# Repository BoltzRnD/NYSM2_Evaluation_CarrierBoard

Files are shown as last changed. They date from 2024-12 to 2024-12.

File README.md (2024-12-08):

# NYSM.2 Evaluation Carrier Board

### Note - This repository hosts the design files for the evaluation carrier board only, to explore the NYSM.2 Stepper Driver module please refer to NYSM.2 repository here -
<a href="https://github.com/BoltzRnD/NYSM2_Open_Stepper_Standard">NYSM.2 Open Modular Stepper Driver Interface Standard by Boltz R&D </a>
</br>

### Join our Discord Server to Discuss NYSM.2 -



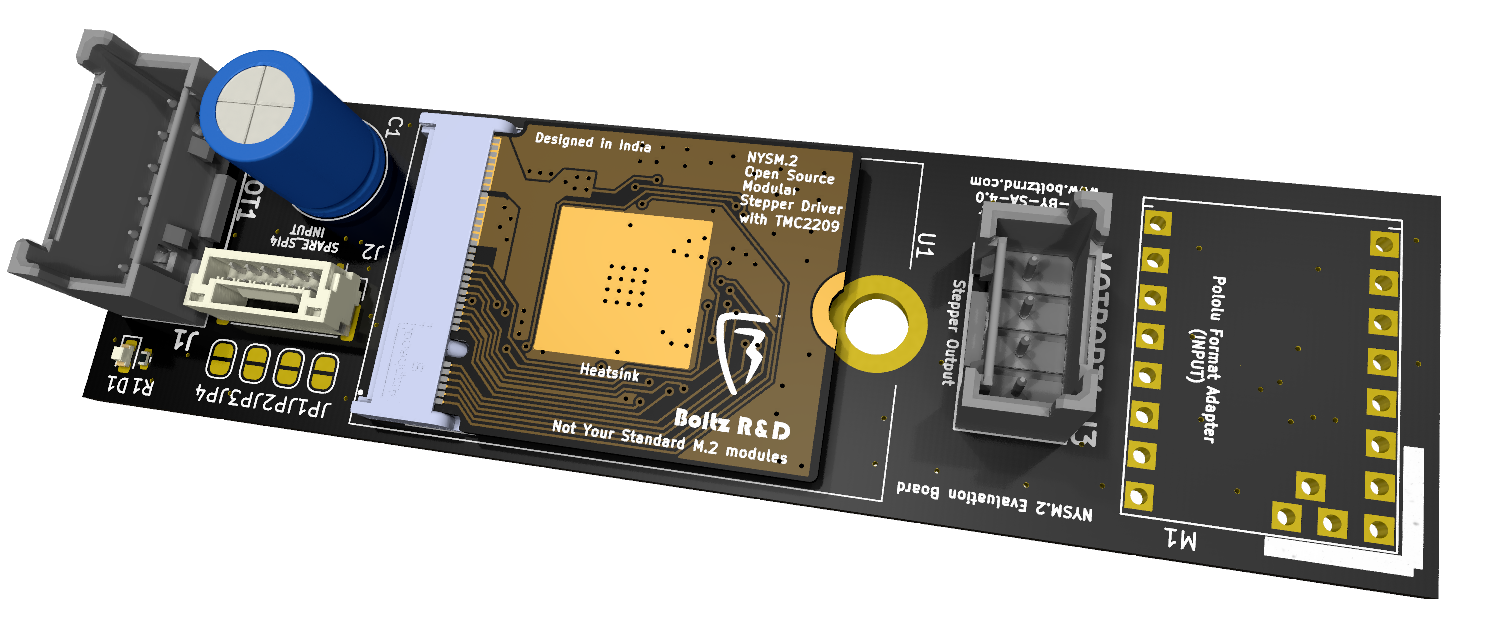
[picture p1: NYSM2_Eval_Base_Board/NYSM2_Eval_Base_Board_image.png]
NYSM.2


# NYSM.2 Open Stepper Standard
## Not Your Standard M.2
### "Not Your Standard M.2" is literally not your standard m.2 interface, and is a new open-source stepper motor driver board that utilizes the M.2 interface to control motors using the TMCxx and all other stepper drivers.

Modular stepper drivers are far superior than traditional pololu footprints as it has

1. Poka-yoke installations: The Key's in the interfaces makes sure that you never mess up installation orientations of the driver

apart from this NYSM.2 extends beyond these to provide more features as below:

1. physical locking mechanisms: to make sure drivers are locked in when In operation.

2. Horizontal installation: instead of vertical mounting, to not only save space in Z axis, but to also make the system less fragile to accidental damage if stuck by a physical shock.

3. Top and Bottom Installations: since NYSM.2 utilizes SMD and single layer mounted connectors, it means that it is possible to add by design 2 NYSM.2 modules in the same footprint area, drastically reducing the required footprint for more drivers - i.e - 20 drivers in 10 drivers area by installing 10 on top layer and 10 on bottom.

4. highly cost effective: since M.2 is a widely available standard with high MOQs already flooding the industry, the M.2 connectors can be integrated at very low costs into your design, where the stepper card doesn't even need a connector as it uses an edge connector built into the PCB only. in comparison to other modular standards that uses custom repurposed obsolete connector that has low manufacturing volumes. With NYSM.2 we can adopt a modular standard at almost same cost of a traditional pololu stepper drivers.

5. Powerful in terms of power: NYSM.2 utilizes 8 contacts(0.5A per pin) per power connection to deliver a whopping **4A** to the motors, that too at **24V**, that totals to **96W** per driver.
moreover it is theoretically possible to get more power out of it by increasing the voltages.

But that is not the best thing about NYSM.2 standard, the only best thing about it is only and only it's open source nature and GPL V3 license, that allows creators, hobbyist and manufacturers worldwide to move to a new and open modular stepper driver interface standard.
unlike other modular stepper interfaces, this interface is open inside out, and is not designed to lock you into single specific manufacturer's ecosystem. and is made for the world to use.

## The NYSM.2 Standard Pinout Format

## Pinout Table

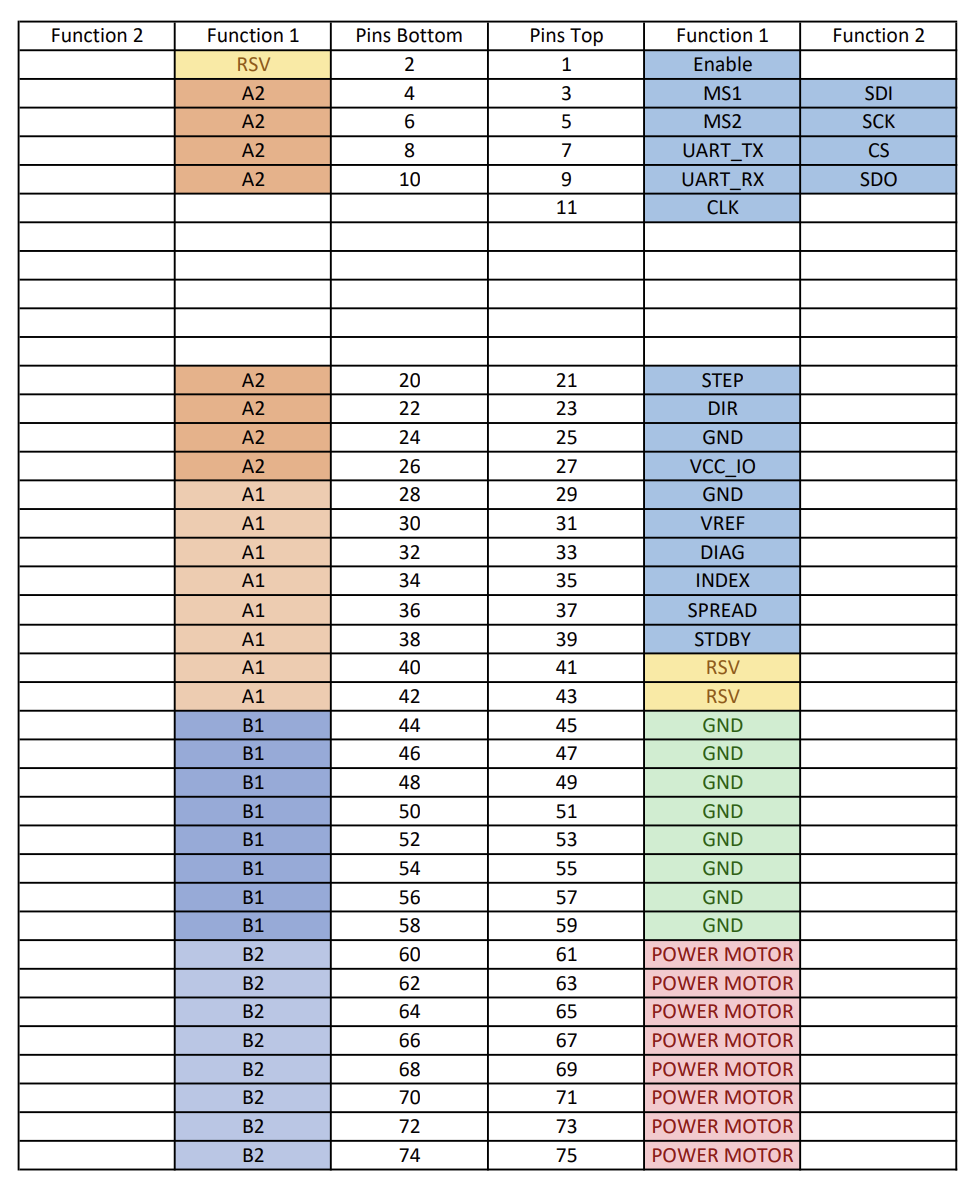
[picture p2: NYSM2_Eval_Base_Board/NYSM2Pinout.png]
NYSM.2 Pinout


| Pin Name | Pin Number | Description 
|---|---|---|
| EN | 1 | Enable/Disable Stepper Driver
| MS1 | 3 | Microstep Selection Pin 1 / CFG1 / SDI
| MS2 | 5 | Microstep Selection Pin 2 / CFG2 / SCK
| UART_TX | 7 | UART Transmission (Communication) / CFG 3 / CS
| UART_RX | 9 | UART Receive (Communication) / CFG0 / SDO
| CLK | 11 | CLK input 
| STEP | 21 | STEP input 
| DIR | 23 | DIR input 
| GND | 25 | Ground 
| VCC_IO | 27 | 3.3V to 5V IO supply voltage for all digital pins (does not supply IC logic part).
| GND | 29 | Ground 
| VREF | 31 | Analog reference voltage for current scaling or reference current for use of internal sense resistors
| DIAG | 33 | Diagnostic and StallGuard output
| INDEX | 35 | Configurable index output. Provides index pulse.
| SPREAD | 37 | Chopper mode selection: Low=StealthChop, High=SpreadCycle (may be left unconnected)
| STDBY | 39 | STANDBY input  
| GND | 45, 47, 49, 51, 53, 55, 57, 59 | Ground/PSU Negative (0.5A per pin, 4A Total)
| POW_MOT | 61, 63, 65, 67, 69, 71, 73, 75 | Motor supply voltage (0.5A per pin, 4A Total)
| A2 | 4, 6, 8, 10, 20, 22, 24, 26 | Motor coil A output 2 (0.5A per pin, 4A Total)
| A1 | 28, 30, 32, 34, 36, 38, 40, 42 | Motor coil A output 1 (0.5A per pin, 4A Total)
| B1 | 44, 46, 48, 50, 52, 54, 56, 58 | Motor coil B output 1 (0.5A per pin, 4A Total)
| B2 | 60, 62, 64, 66, 68, 70, 72, 74 | Motor coil B output 2 (0.5A per pin, 4A Total)

# Manufacturing and other design considerations

Please take special care to follow these points when manufacturing the NYSM2 Boards
1. You'll need Connector assemblies to interface the board specifically - GHR-06V-S and 511630400 Connectors, which are the same cables used in SmartPrintCoreH7x, please refer to Connector BOM from SmartPrintCoreH7x for more details
2. Set the solder jumpers as per your convenience especially for uart lines, just like your regular pololu drivers, please feel free to browse schematics for reference or directly reach out to our discord server for help.

# License
NYSM.2 standard pinout and NYSM.2 TMC2209 Carrier Board contributed by Boltz R&D is licensed under GPL V3, and is owned by the community and everyone.
Also while the standard is open(i.e - The standard pinout sequence on M.2 Key B and it's derivatives only, that means proprietary manufacturers needs to be compliant to GPLV3 for only the pinout.),
you can integrate it into your proprietary designs as long as the NYSM.2 section of your design respects the license.
We invite all creators, hobbyist, and manufacturers to utilize the standard and the design.

# Key Features for this NYSM.2 Carrier Board:
* NYSM.2 Interface: Compact, modular design that fits into M.2 slots, making it easy to install and maintain.
* The Connectors and pinouts used in the design plugs directly into Smartmotor ports and any SPI Port of SmartPrintCoreH7x, and with just minor pinout configurations in the firmware, it's up and running.

## Assembly and Setup

1. **Step 1**: Insert the **NYSM.2** board into the M.2 slot.
2. **Step 2**: Connect your stepper motor wires to the appropriate output terminals i.e- Smartmotor ports and any spi port(which can also act as a uart port).
3. **Step 3**: Configure your firmware (e.g., **Marlin** or **Klipper**) to control the TMC2209 driver.
4. **Step 4**: Power on the system, and your motors are ready.

## Getting Started on Development:

Clone the repository:  
`git clone https://github.com/BoltzRnD/NYSM2_Evaluation_CarrierBoard`

# Join the Community
We are actively looking for contributors to help us enhance this project. You can join our community to discuss ideas, report bugs, or request features:

- **Discord**: [Join us here](https://discord.gg/xWGaHd83Hs)
- **Email**: info@boltzrnd.com

# Future Plans
- **Custom Heatsink Designs**.
- **Extended Compatibility**: support for other stepper driver like TMC5160 and TMC2130.

# Disclaimer
The **NYSM.2 standard and NYSM.2 Carrier board** is provided as-is without any warranties. Boltz R&D is not responsible for any damages or issues that may arise from the use of this board.

    NYSM.2 standard
    Copyright (C) 2024 Boltz R&D

    This Project/Open Standard is free: you can redistribute it and/or modify
    it under the terms of the GNU General Public License as published by
    the Free Software Foundation, either version 3 of the License, or
    (at your option) any later version.

    This is distributed in the hope that it will be useful,
    but WITHOUT ANY WARRANTY; without even the implied warranty of
    MERCHANTABILITY or FITNESS FOR A PARTICULAR PURPOSE.  See the
    GNU General Public License for more details.

    You should have received a copy of the GNU General Public License
    along with this program.  If not, see <https://www.gnu.org/licenses/>.

Contact : info@boltzrnd.com

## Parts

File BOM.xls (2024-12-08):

Comment | Designator | Footprint | JLCPCB Part #
MOTPORT1 | J3 | connectorslibrary:53375-0410 | C327537
SMRTMOT1 | J1 | connectorslibrary:53375-0610 | C504969
~ | U1 | MDT275B03001:AMPHENOL_MDT275B03001 | C2761344
M2Mount | H1 | M2Mount | C5301790
POW-MOT | D1 | LED_SMD:LED_0603_1608Metric | C72038
4.7K | R1 | Resistor_SMD:R_0402_1005Metric | C140158
SPARE_SPI4 | J2 | Connector_JST:JST_GH_BM06B-GHS-TBT_1x06-1MP_P1.25mm_Vertical | C189892
100uF50V | C1 | Capacitor_THT:C_Radial_D8.0mm_H11.5mm_P3.50mm | C2960238

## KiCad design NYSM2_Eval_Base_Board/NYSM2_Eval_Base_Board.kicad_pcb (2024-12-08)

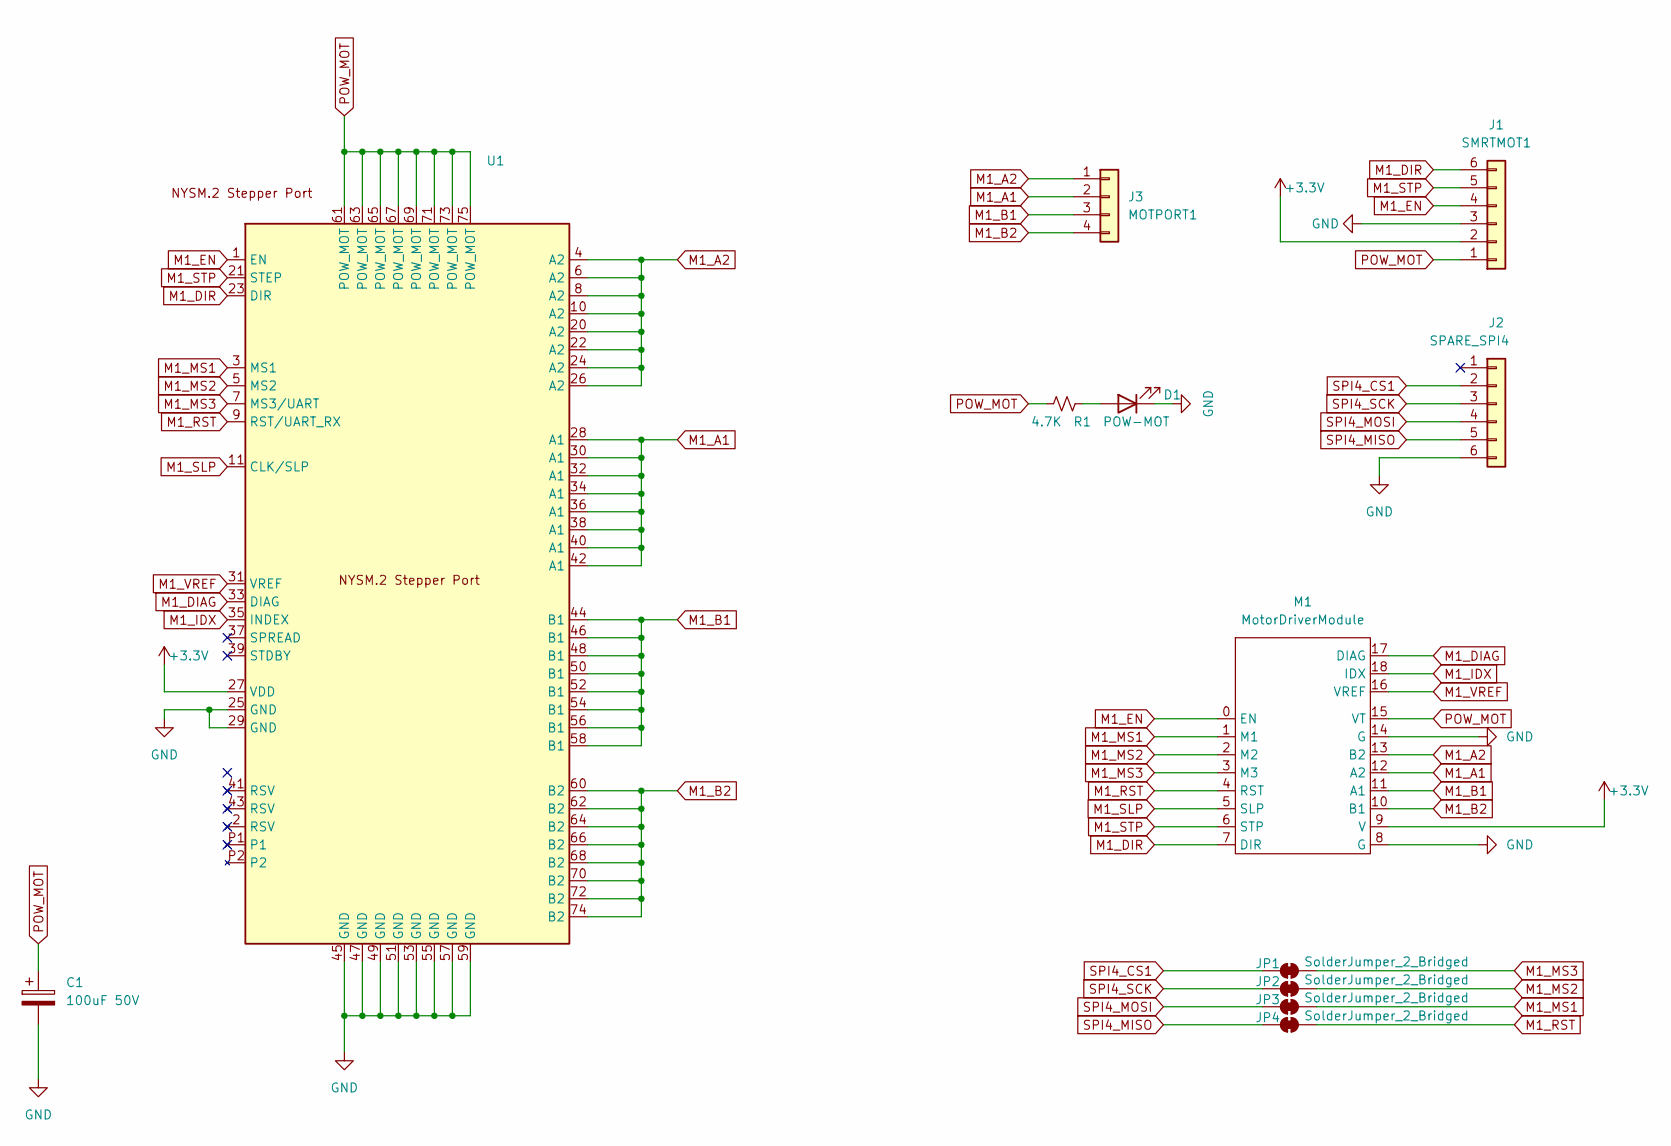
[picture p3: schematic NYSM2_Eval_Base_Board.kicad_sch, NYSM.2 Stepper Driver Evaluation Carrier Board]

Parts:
C1: 100uF 50V; C_Radial_D8.0mm_H11.5mm_P3.50mm
D1: POW-MOT; LED_0603_1608Metric; Manufacturer_Part_Number B1911PG--20D000514U1930
J1: SMRTMOT1; 53375-0610; Manufacturer_Part_Number 53375-0610
J2: SPARE_SPI4; JST_GH_BM06B-GHS-TBT_1x06-1MP_P1.25mm_Vertical; Manufacturer_Part_Number BM06B-GHS-TBT
J3: MOTPORT1; 53375-0410; Manufacturer_Part_Number 53375-0410
JP1, JP2, JP3, JP4: SolderJumper_2_Bridged; SolderJumper-2_P1.3mm_Bridged_RoundedPad1.0x1.5mm
M1: MotorDriverModule; MotorDriverModuleBase
R1: 4.7K; R_0402_1005Metric; Manufacturer_Part_Number CRGCQ0402J4K7
U1: AMPHENOL_MDT275B03001; Manufacturer_Part_Number AS0BC21-S30BB-7H

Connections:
+3.3V: J1.2, M1.9 (V), U1.27 (VDD)
GND: C1.2, D1.1 (K), J1.3, J2.6, M1.8 (G), M1.14 (G), U1.25 (GND), U1.29 (GND), U1.45 (GND), U1.47 (GND), U1.49 (GND), U1.51 (GND), U1.53 (GND), U1.55 (GND), U1.57 (GND), U1.59 (GND)
M1_A1: J3.2, M1.12 (A2), U1.28 (A1), U1.30 (A1), U1.32 (A1), U1.34 (A1), U1.36 (A1), U1.38 (A1), U1.40 (A1), U1.42 (A1)
M1_A2: J3.1, M1.13 (B2), U1.4 (A2), U1.6 (A2), U1.8 (A2), U1.10 (A2), U1.20 (A2), U1.22 (A2), U1.24 (A2), U1.26 (A2)
M1_B1: J3.3, M1.11 (A1), U1.44 (B1), U1.46 (B1), U1.48 (B1), U1.50 (B1), U1.52 (B1), U1.54 (B1), U1.56 (B1), U1.58 (B1)
M1_B2: J3.4, M1.10 (B1), U1.60 (B2), U1.62 (B2), U1.64 (B2), U1.66 (B2), U1.68 (B2), U1.70 (B2), U1.72 (B2), U1.74 (B2)
M1_DIAG: M1.17 (DIAG), U1.33 (DIAG)
M1_DIR: J1.6, M1.7 (DIR), U1.23 (DIR)
M1_EN: J1.4, M1.0 (EN), U1.1 (EN)
M1_IDX: M1.18 (IDX), U1.35 (INDEX)
M1_MS1: JP3.2 (B), M1.1 (M1), U1.3 (MS1)
M1_MS2: JP2.2 (B), M1.2 (M2), U1.5 (MS2)
M1_MS3: JP1.2 (B), M1.3 (M3), U1.7 (MS3/UART)
M1_RST: JP4.2 (B), M1.4 (RST), U1.9 (RST/UART_RX)
M1_SLP: M1.5 (SLP), U1.11 (CLK/SLP)
M1_STP: J1.5, M1.6 (STP), U1.21 (STEP)
M1_VREF: M1.16 (VREF), U1.31 (VREF)
unnamed: D1.2 (A), R1.1
POW_MOT: C1.1, J1.1, M1.15 (VT), R1.2, U1.61 (POW_MOT), U1.63 (POW_MOT), U1.65 (POW_MOT), U1.67 (POW_MOT), U1.69 (POW_MOT), U1.71 (POW_MOT), U1.73 (POW_MOT), U1.75 (POW_MOT)
SPI4_CS1: J2.2, JP1.1 (A)
SPI4_MISO: J2.5, JP4.1 (A)
SPI4_MOSI: J2.4, JP3.1 (A)
SPI4_SCK: J2.3, JP2.1 (A)

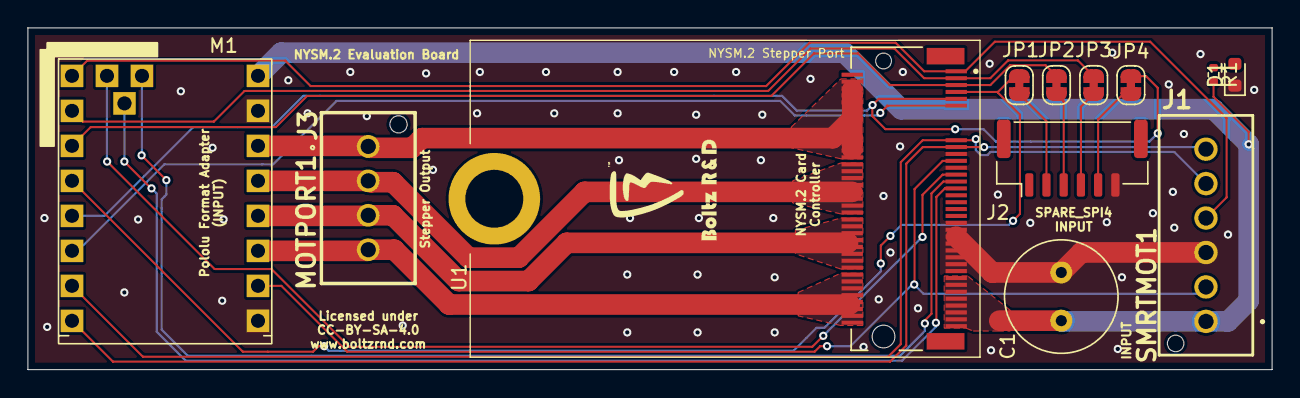
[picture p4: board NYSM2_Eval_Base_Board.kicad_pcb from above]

Board: 2 copper layers, 90.3 x 24.8 mm, 12 parts (0 on the bottom side), 23 nets.

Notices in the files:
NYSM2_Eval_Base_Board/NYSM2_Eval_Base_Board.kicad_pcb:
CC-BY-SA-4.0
